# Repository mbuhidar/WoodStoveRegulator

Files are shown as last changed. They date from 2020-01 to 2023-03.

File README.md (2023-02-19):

# WoodStoveRegulator 2.3 - Arduino Powered Stove Damper Regulation

 System drives an Arduino microcontroller-based device that automatically 
 controls the air damper position on a wood stove in order to maintain a 
 constant exhaust pipe temperature.  
 
 System inputs: 
  1) Exhaust pipe temperature as measured by a thermocouple 
  mounted directly to the exhaust pipe (K-type thermocouple with 
  d-ring end connected to Arduino via MAX6675 module.
  2) A variable knob that controls LCD brightness (10K potentiometer).
  3) A variable knob that manually controls the stove damper 
  position between 0% and 100% for the first half of the knob rotation range
  and places the control system in automatic mode for potentiometer settings
  greater than half the rotation range. In automatic mode, the knob controls
  setting the stove target temperature between 100 C (212 F) and 200 C (392 F). 

 System outputs:
  1) LCD display showing:
     a) Exhaust pipe temperature and target temperature on 1st line of LCD.
     b) Alternating message on 2nd line of LCD showing A. damper / 
     potentiometer position and B. damper / mode - auto or manual.  
  2) Physical control of the stove air damper is transmitted from a 
     servo motor mounted inside the control unit with force and 
     position being transferred via sheathed control cable connected 
     between the servo and the stove damper lever.
  3) Passive buzzer that provides an audible alert when wood needs to be added
     or when stove damper will be closed due to end of fire event.

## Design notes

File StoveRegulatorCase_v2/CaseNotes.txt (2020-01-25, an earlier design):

3D Printed Case for Wood Stove Regulator

Configuration is wall mounted case with Arduino ports facing downward,
LCD screen centered vertically on the top case with control knobs below it.
Control cable exits the case on the bottom of the case as mounted.

Modeled using Autodesk Fusion 360 and printed using PLA filament.
Case was modified from:
Arduino-UNO-DIN-Case (6TE) (http://www.thingiverse.com/thing:3402441)
Changes to case and other printed parts:
- made bottom deeper to accommodate a breadboard shield for the Arduino
- added support ribbing to the top case to improve print quality
- changed holes and clamp in case to work with the push/pull cable and the thermocouple wire
- added a support mounting surface for the thermocouple amplifier
- added mounting pillars to support the servo inside the bottom case
- added a new wall mount and a cable connection piece for the wood stove damper

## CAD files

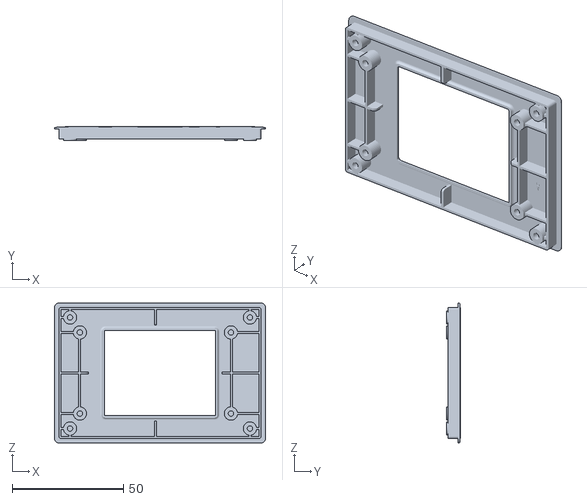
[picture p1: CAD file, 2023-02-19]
StoveRegulatorCase_v3/2.4-Bezel.STL
95.0 x 6.20 x 63.0

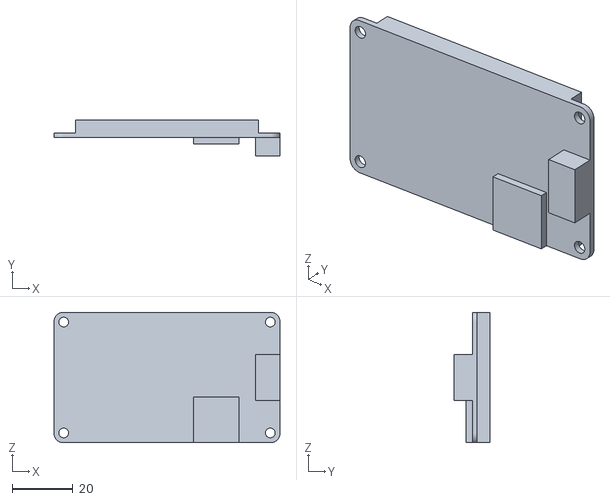
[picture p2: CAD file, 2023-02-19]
StoveRegulatorCase_v3/2.4-Display.STL
74.4 x 11.8 x 42.9

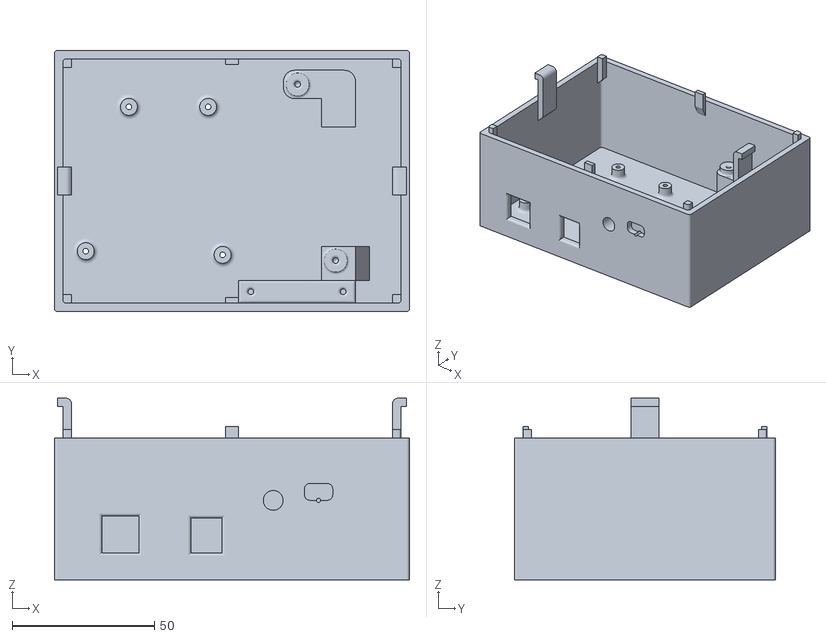
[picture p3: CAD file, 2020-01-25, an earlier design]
StoveRegulatorCase_v2/bottom_mod v21.stl
125.0 x 92.0 x 64.0

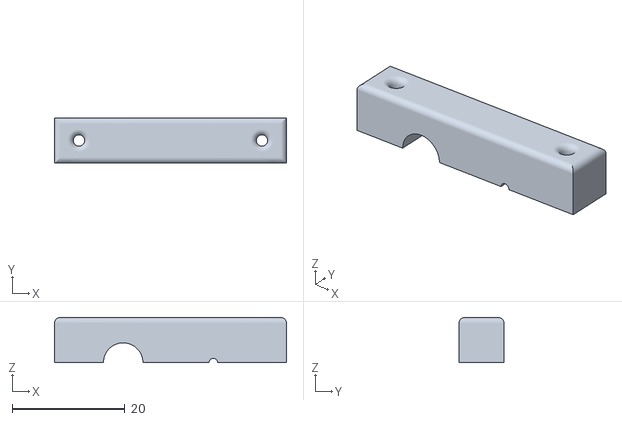
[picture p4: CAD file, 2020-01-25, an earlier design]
StoveRegulatorCase_v2/cable_clamp v1.stl
41.2 x 8.00 x 8.00

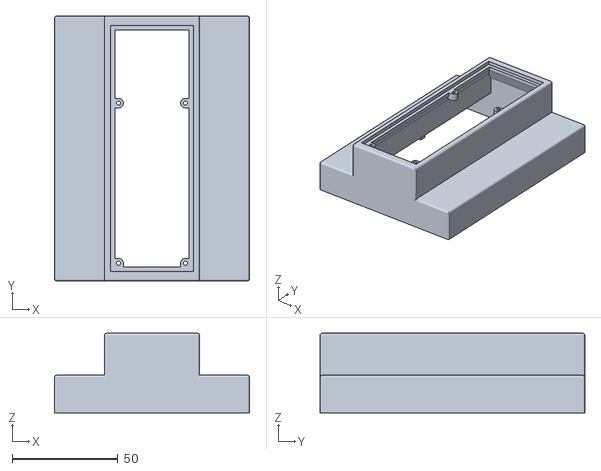
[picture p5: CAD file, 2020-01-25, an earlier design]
StoveRegulatorCase_v2/top_mod v2.stl
92.0 x 125.0 x 37.5

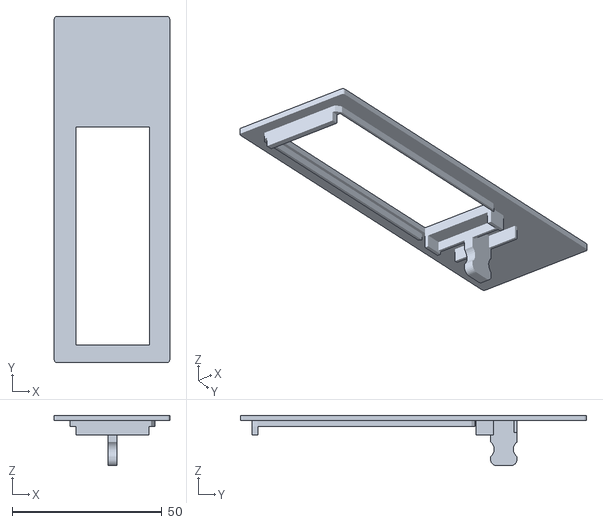
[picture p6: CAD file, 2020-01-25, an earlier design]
StoveRegulatorCase_v2/display_mod v1.stl
38.6 x 115.6 x 16.8

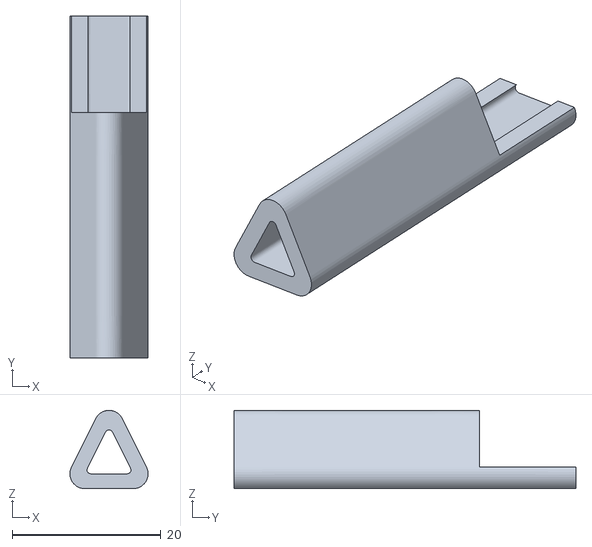
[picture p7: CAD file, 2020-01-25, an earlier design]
StoveRegulatorCase_v2/lever_adapter v1.stl
10.5 x 46.0 x 10.5

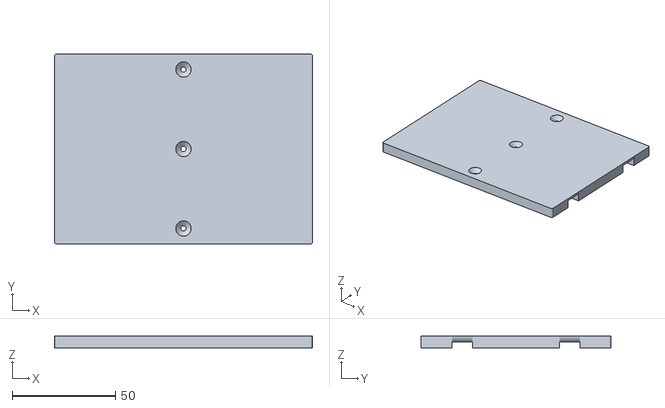
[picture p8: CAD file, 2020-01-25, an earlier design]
StoveRegulatorCase_v2/new_mount v2.stl
125.0 x 92.0 x 6.00

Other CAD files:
StoveRegulatorCase_v2/bottom_mod v21.f3d
StoveRegulatorCase_v2/cable_clamp v1.f3d
StoveRegulatorCase_v2/display_mod v1.f3d
StoveRegulatorCase_v2/lever_adapter v1.f3d
StoveRegulatorCase_v2/new_mount v2 v2.f3d
StoveRegulatorCase_v2/top_mod v2.f3d

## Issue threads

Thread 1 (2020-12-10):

Change left input knob to control temperature setting vs display brightness

mbuhidar, 2020-12-10:
Stove temp range can be 200-400 F, currently hard coded to 250 F.  Add control via left knob and add display for temperature set point.

Display setting can be hard coded vs using input pot.

mbuhidar, 2020-12-14:
Left potentiometer is does not act as an input for the controller, but acts as a variable resistor directly tied to the LCD brightness pin.  Would need to add another pot or repurpose the left knob and hardwire an appropriate resistor to manage LCD brightness.  Adjusted the hard coded set temperature to 275F in the meantime to raise the heat output of the stove.

mbuhidar, 2020-12-27:
May address this after winter if I rebuild the hardware.  In the meantime, will close this issue and open a new one to make the right pot act as a multi-function input to adjust temperature set point.

Closed 2020-12-27.

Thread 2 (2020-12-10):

After days of operation, controller went into 'stove empty - end fire' mode and opened damper while wood full and actively burning

mbuhidar, 2020-12-10:
This function was intended to be disabled, so need to understand how it was executed.  Suspect PID value accumulations over many days of continuous operation.

mbuhidar, 2020-12-10:
Switching from auto to manual mode and back to auto does not reset to eliminate this issue.  A power cycle was required to resolve the issue.

mbuhidar, 2020-12-14:
Completely rewrote the section of code that manages this functionality for v2.0 to resolve the issue.

Closed 2020-12-14.

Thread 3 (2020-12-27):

Add temperature set point adjustment feature using only available controller input - the right hand potentiometer.

mbuhidar, 2020-12-27:
Stove exhaust stack temp range can be 200-400 F, currently hard coded to 275 F in V2.0. Add control functionality via right knob via new 'adjust temperature set point' mode.  Need to determine user-initiated sequence to enter this mode and adjust the set point.

mbuhidar, 2021-01-18:
Feature to control set temperature was implemented by using the upper 50% of the potentiometer range for setting target temp and using the lower 50% of the range for manual damper control.  Temperature range available is set to 100 C (212 F) - 200 C (392 F).

Also, remapped the output display to add the temperature set point along with the prior messages.  Second line is set to rotate messages so all messages can be displayed.

Closed 2021-01-18.

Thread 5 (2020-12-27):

Add a function to check if the stove has been refilled with wood and is building temperature from low towards set point.

mbuhidar, 2020-12-27:
Current v2.0 code accumulates the integral parameter the entire time the exhaust stack temp is rising from a low temp towards the set point temp after a refill.  This results in the controller going into 'fill' mode inappropriately and in some cases, the controller can go into 'end' mode even when the temp is rising.  This is caused by the integral parameter building past the individual triggers for those two modes.

When the controller enters either of these two modes, the controller does not re-enter 'auto' mode until the temp reaches the set point.  This results in significant temp overshoot.  Even if the controller doesn't enter one of these modes, the integral windup can cause overshoot in 'auto' mode.

This new function / feature is intended to check for temp rise that would indicate stove refill and temperature build towards set point.  If refill condition is detected, the integral term should be reset to zero in order to prevent integral windup.

mbuhidar, 2020-12-31:
Added function that holds/updates an array of past six temp readings and compares average of first 3 to average of last 3 to determine if wood has been refilled.  The function is called to check status throughout the main loop function.

Closed 2020-12-31.

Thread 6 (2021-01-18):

Add physical switch to toggle between manual and auto mode.

mbuhidar, 2021-01-18:
Due to lack of physical user inputs to the controller, the single controller-attached potentiometer is being overused for mode and range selection.  The v2.2 code uses the upper half of the pot range to set the target temp in auto mode and the lower half of the pot range sets the damper position in manual mode.  The input range available is not ideal to control these modes and usage requires 'expert' knowledge of how the one knob works.

Need to add a physical input (push button switch?) to set and / or control auto mode vs manual mode.

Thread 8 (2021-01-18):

Rebuild controller using improved components and more robust internal connections

mbuhidar, 2021-01-18:
Current controller is printed with white filament and the LCD light and internal power supply lights bleed through the case.  Reprint case in black with provision for additional input button or pot per Issue #6.

Current internal connections are basic breadboard type connections.  These connections should made with soldered wires or a custom PCB.

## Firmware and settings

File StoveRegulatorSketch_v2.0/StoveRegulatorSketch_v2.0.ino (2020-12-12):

/*
 Wood Stove Regulator - Version 2.0
 by Michael Buhidar (GitHub: buhidar)

 with thanks to philco for many of the foundational ideas for this project
 (https://www.instructables.com/id/Wood-Stove-Regulator/)

 Sketch drives an Arduino microcontroller based system that auomatically 
 controls the air damper on a wood stove in order to maintain a 
 constant exhaust pipe temperature.  
 
 System inputs: 
  1) Exhaust pipe temperature as measured by a thermocouple 
  mounted directly to the exhaust pipe (sensor is K-type thermocouple with 
  d-ring end connected to Arduino via MAX6675 module.
  2) A variable knob that controls LCD brightness (10K potentiometer).
  3) A variable knob that manually controls the stove damper 
  position between 0% and 100% and places the control system in 
  automatic mode at potentiometer setting above 100% (10K potentiometer). 
  4) FUTURE FEATURE: A variable knob that controls the temperature target for
  the stove exhaust pipe.  Range from 200-400F.

 System outputs:
  1) LCD display showing:
     a) Exhaust pipe temperature on 1st line of LCD.
     b) Stove control knob potentiometer setting on 1st line of LCD.
     c) Damper position when in manual mode or in automatic
        mode while stove has adequate wood loaded on 2nd line of LCD.
     d) Message to refill the stove on 2nd line if wood is low or
        message that fire is ended if wood is not refilled.
  2) Physical control of the stove air damper transmitted from a 
     servo motor mounted inside the control unit with force and 
     position being transferred via sheathed control cable connected 
     between the servo and the stove damper lever.
  3) Passive buzzer that provides an audible alert when wood needs to be added
     or when stove damper will be closed due to end of fire event.

 
     
*/

// Include libraries for max6675, servo, LCD, and math.
#include <max6675.h>
#include <Servo.h>
#include <LiquidCrystal.h>
#include <math.h>

// Thermocouple pins mapping:
int thermoCsPort = 6;               // CS pin on MAX6675; chip select
int thermoSoPort = 7;               // SO pin of MAX6675; serial output
int thermoSckkPort = 8;             // SCK pin of MAX6675; serial clock input

// int units = 1;                      // Toggle for readout temp units (0 = ˚F, 1 = ˚C) 
float error = 0.0;                  // Temperature compensation error

// Buzzer variables:
int buzzerPort = 9;                 // Buzzer port
int buzzerRefillFrequency = 1900;   // Buzzer tone frequency for refill alarm
int buzzerRefillRepeat = 3;         // Number of refill alarm tones
int buzzerRefillDelay = 1000;       // Delay of refill alarm tone
int buzzerCloseFrequency = 950;    // Buzzer tone frequency for end of fire damper close alarm
int buzzerCloseRepeat = 2;          // Number of tones for end of fire damper close alarm
int buzzerCloseDelay = 2000;        // Delay of tone for end of fire damper close alarm

// Potentiometer variables
int servoPort = 0;
int potPort = 0;

// LCD port variables
int lcdPort1 = 12;
int lcdPort2 = 11;
int lcdPort3 = 5;
int lcdPort4 = 4;
int lcdPort5 = 3;
int lcdPort6 = 2;

// Device objects
Servo myservo;  // create servo object to control the servo
MAX6675 thermocouple(thermoSckkPort, thermoCsPort, thermoSoPort); 
LiquidCrystal lcd(lcdPort1, lcdPort2, lcdPort3, lcdPort4, lcdPort5, lcdPort6);

// Servo settings
float servoCalibration = 1.0;  // 1.0 is neutral cal - adjust value so servo arm drives closed damper when damper variable equals 0 (0%)
float servoOffset = 20;  // offset angle for servo angle adjustment
float servoAngle = 100;  // adjust value to define total angular travel of servo so that cable drives damper from fully opened to fully closed

// Regulation variables (Based on PID):
// damper = kP * errP + kI * errI + kD * errD
// errP = targetTempC - temperature
// errI = errP integral
// errD = errP derivative
int temperature = 0;  // initialize temperature variable for C
int temperatureF = 32; // initialize temperature variable for F - only used for display output
float temperatureMin = 38; // under this temperature (38C = 100F), the regulation starts an integral measure to estimate end of fire and close the damper
float targetTempC = 121.1; // the target temperature as measured by the thermocouple (121.1 C = 250 F)
float errP = 0.0;
float errD = 0.0;
float errI = 0.0;
float errOld = 0.0;
float kP = 5;              // P coefficient of the PID regulation
float kI = 0.0005;         // I coefficient of the PID regulation
float kD = 0.00005;        // D coefficient of the PID regulation

float refillTrigger = 5000;    // refillTrigger used to notify need of a wood refill
float closeTrigger = 15000;    // closeTrigger used to close damper at end of combustion

int pot = 0;
int oldPot = 0;
float potMax = 1023.0;   // Potentiometer calibration
int potRelMax = 100;     // Potentiometer value above which the regulator runs in automatic mode

int angle = 0;
int damper = 0;
int oldDamper = 0;
int diff = 0;
float maxDamper = 100.0;  // Sets maximum damper setting
float minDamper = 0.0;    // Sets minimum damper setting
float zeroDamper = 0.0;   // Sets zero damper setting - note that stove allows some amount of airflow at zero damper

String messageTemp; // Initialize message for temperature output
String messageDamp; // Initialize message for damper setting output

boolean closeBuzzer = true;
boolean refillBuzzer = true;




void setup() {
  Serial.begin(9600);  // opens serial port, sets data rate to 9600 bps
  myservo.attach(10);  // attach servo variable to pin 10
  // move servo from current angle to zero non-abruptly
  ang = myservo.read();
  for (int i = ang; i > 0; i--) {
    myservo.write(ang);
    delay(200);
  myservo.write(0);    // write 0 deg angle to servo after gradual move
  myservo.detach();    // detach servo variable from its pin
  lcd.begin(16, 2);    // initializes 1602 LCD screen for 16 columns and 2 rows
  pinMode(buzzerPort, OUTPUT); // configures buzzer pin as an output
}




void loop() {

  temperature = thermocouple.readCelsius();
  temperatureF = temperature * 9 / 5 + 32;  // convert C to F
  
  delay(500); 
  
  if (temperature == -1) {
    Serial.println("Thermocouple Error!!"); // Temperature is read as -1 and there is a thermocouple error
  } else {

    pot = analogRead(potPort); // reads the value of the potentiometer (value between 0 and 1023)
    pot = map(pot, 0, potMax, 0, 105); // scale potentiometer reading to 0 to 105%; note that setting above 100% invokes automatic mode
    
    if (pot <= potRelMax ) {  
      // Manual damper regulation mode
      errI = 0;  // reset integral term
      errD = 0;  // reset derivative term
      closeBuzzer = true;
      refillBuzzer = true;
      damper = round(pot * maxDamper / 100);  // scales damper setting according to max setting
      messageDamp = "Damper=" + String(damper) + "% Man";
    }

    else
    
    { 
      if (errI < closeTrigger) {
        // Automatic PID regulation
        errP = targetTempC - temperature;  // set proportional term
        errI = errI + errP;                // update integral term
        errD = errP - errOld;              // update derivative term
        errOld = errP;
        // set damper position and limit damper values to physical constraints
        damper = kP * errP + kI * errI + kD * errD;
        if (damper < minDamper) damper = minDamper;
        if (damper > maxDamper) damper = maxDamper;


        // Close and end fire
        // if (errI >= closeTrigger) errI = closeTrigger;
        // 
        if (temperature < temperatureMin) errI = 0;  // reset errI if temperature is higher than minimum cutoff temperature
        // if (errI >= closeTrigger) damper = zeroDamper;

        messageDamp = "Damper=" + String(damper) + "% Auto";
        //Refill Alarm
        if (errI > refillTrigger) {
          messageDamp = "Damper=" + String(damper) + "% Fill";
          if (refillBuzzer) {
            for (int i = 0; i < buzzerRefillRepeat; i++) {
              tone(buzzerPort, buzzerRefillFrequency);
              delay(buzzerRefillDelay);
              noTone(buzzerPort);
              delay(buzzerRefillDelay);
            }
            refillBuzzer = false;
          }
          if (temperature > targetTempC) {
            errI = 0;
            errD = 0;
            refillBuzzer = true;
          }
        }

      }

      else {
        // Close Damper if end of combustion
        messageDamp = "Damper=" + String(damper) + "% End";

        if (closeBuzzer) {
          for (int i = 0; i < buzzerCloseRepeat; i++) {
            tone(buzzerPort, buzzerCloseFrequency);
            delay(buzzerCloseDelay);
            noTone(buzzerPort);
            delay(buzzerCloseDelay);
          }
          closeBuzzer = false;
        }
      }
    }

    // Display messages on LCD
    lcd.clear();
    lcd.setCursor(0, 0);
    messageTemp = "Tmp=" + String(temperatureF) + "F" + " Pot=" + round(pot) + "%";
    lcd.print(messageTemp);
    lcd.setCursor(0, 1);
    lcd.print(messageDamp);

    // Serial Plotter
    Serial.print(round(damper/maxDamper * 100));
    Serial.print(",");
    Serial.print(temperatureF);
    Serial.print(",");
    Serial.print(errP);
    Serial.print(",");
    Serial.print(errI);
    Serial.print(",");
    Serial.print(errD);
    Serial.print(",");    
    Serial.println();

    // Turn servo only for more than 2° delta
    diff = damper - oldDamper;
    if (abs(diff) > 2) {
      lcd.print(" x");
      delay(500);
      myservo.attach(10);
      if (diff > 2) {
        for (int i = 0; i < diff; i++) {
            angle = (oldDamper + i + 1) * servoAngle / (maxDamper * servoCalibration) - servoOffset;
            myservo.write(angle);
            delay(200);
          }
      }
      
      if (diff < 2) {
        for (int i = 0; i < abs(diff); i++) {
            angle = (oldDamper - i - 1) * servoAngle / (maxDamper * servoCalibration) - servoOffset;
            myservo.write(angle);
            delay(200);
          }
      }
          
      myservo.detach();

      oldPot = pot;
      oldDamper =  damper;
    }
    delay(4000);
  }
}

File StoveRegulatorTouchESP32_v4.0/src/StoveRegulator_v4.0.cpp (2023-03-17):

/*
 Wood Stove Regulator - Version 4.0 
 Copyright (C) 2020  Michael Buhidar (GitHub: mbuhidar)
 
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
 For a copy of the GNU General Public License, 
 see <https://www.gnu.org/licenses/>.

 With thanks to philco for many of the foundational ideas for this project
 (https://www.instructables.com/id/Wood-Stove-Regulator/)

 The code drives an ESP32 microcontroller based system that automatically 
 controls the air damper on a wood stove in order to maintain a constant
 exhaust pipe temperature.  
 
 System inputs and outputs: 

  1) Exhaust pipe temperature as measured by a thermocouple mounted directly to
     the exhaust pipe. Sensor is K-type thermocouple with a ring attach end
     connected to an Arduino (Uno in this case) via MAX6675 module.

  2) A touch screen display (Nextion NX3224T024_011) that has two modes - 
     automatic and manual.  

     - Automatic Mode: 
          Screen displays the damper position as a percentage (0-100%), the
          exhaust pipe temperature as an integer (deg F), and the target
          temperature as an integer (deg F). The screen also has in input
          slider bar that can be used to set the target temperature. The damper
          position is automatically controlled by the Arduino microcontroller
          based on the exhaust pipe temperature in this mode. There is a button
          that can be pressed to move to manual mode and display the manual
          mode screen.  
     - Manual Mode:
          Screen displays the damper position as a percentage (0-100%) and the
          exhaust pipe temperature as an integer (deg F). The target
          temperature is greyed out in this mode since it cannot be set on this
          screen. The damper position in this mode is is directly controlled by
          input slider bar on the screen. There is a button that can be pressed
          to move to automatic mode and display the automatic mode screen.
     - TODO: Both modes:
          There is an indicator that flashed when wood needs to be added to the 
          stove. A buzzer is also used to provide an audible alert when wood
          needs to be added.

  3) Physical control of the stove air damper transmitted from a servo motor 
     mounted inside the control unit with force and position being transferred
     via sheathed control cable connected between the servo and the stove
     damper lever.

  4) TODO: Passive buzzer that provides an audible alert when wood needs to be
     added or when stove damper will be closed due to end of fire event.
*/

// ****************************************************************************
// Note: This code is written for the Arduino Uno microcontroller, however,
// more than one hardware serial bus is needed for this project if serial
// output for data analysis is needed. The Arduino Uno only has one hardware
// serial bus. Code could be used for other Arduino microcontrollers that have
// more than one hardware serial bus, but the code would need to be modified.
// ****************************************************************************

// Include libraries for Arduino, max6675, servo, math, and software serial.

#include <Arduino.h>
#include <max6675.h>
#include <Servo.h>
#include <math.h>

// ****************************************************************************
// Device setup and initialization:
// ****************************************************************************

// Software Serial pin mapping variables:
const int rxPort = 10;               // RX pin on Arduino
const int txPort = 11;               // TX pin on Arduino

// Thermocouple pin mapping variables and compensation error variable:
const int thermoCsPort = 6;         // CS pin on MAX6675; chip select
const int thermoSoPort = 7;         // SO pin of MAX6675; serial output
const int thermoSckkPort = 8;       // SCK pin of MAX6675; serial clock input
float error = 0.0;                  // Temperature compensation error

// Buzzer setup variables:
/*
// Buzzer port id
int buzzerPort = 9;
// Buzzer tone frequency for refill alarm
int buzzerRefillFrequency = 1900;
// Number of refill alarm tones
int buzzerRefillRepeat = 3;
// Delay between refill alarm tones
int buzzerRefillDelay = 1000;
// Buzzer tone frequency for end of fire damper close alarm
int buzzerEndFrequency = 950;
// Number of tones for end of fire damper close alarm
int buzzerEndRepeat = 2;
// Delay of tone for end of fire damper close alarm
int buzzerEndDelay = 2000;
*/

// Device objects - create servo and thermocouple objects 
Servo myservo;
MAX6675 thermocouple(thermoSckkPort, thermoCsPort, thermoSoPort); 
SoftwareSerial Serial2(rxPort, txPort); // RX, TX

// Servo calibration settings:
// Servo rate calibration: neutral calibration is 1.0 - adjust value so servo
// arm drives closed damper when damper variable equals 0 (0%)
float servoCalibration = 1.0;
// offset angle for servo angle adjustment
float servoOffset = -20;
// adjust value to define total angular travel of servo so that cable drives
// damper from fully opened to fully closed
float servoRange = 100;

// Temperature variables:       
// Initialize temperature variable (50F = 10C)
int tempF = 50;
// Under this temperature (100F = 38C), the regulation closes the damper
// if end of fire conditions are met
int tempFMin = 100;
// Target temperature (275F = 135C)
int targetTempF = 275;

// PID regulation variables:
float errP = 0.0;          // initialize the proportional term
float errD = 0.0;          // initialize the derivative term
float errI = 0.0;          // initialize the integral term
float errOld = 0.0;        // initialize term used to capture prior cycle ErrP
float kP = 5.0;            // P coefficient of the PID regulation
float tauI = 1000;           // Integral time constant (sec/repeat)
float tauD = 5;              // Derivative time constant (sec/reapeat)
float kI = kP/tauI;        // I coefficient of the PID regulation
float kD = kP/tauD;        // D coefficient of the PID regulation

// Refill and end of fire variables:
// refillTrigger used to notify need of a wood refill
//float refillTrigger = 5000;
// closeTrigger used to close damper at end of combustion
float endTrigger = 25000;

// Damper variables:
int angle = 0;
int damper = 0;
int targetDamper = 0;
int diff = 0;
float maxDamper = 100;  // Sets maximum damper setting
float minDamper = 0.0;    // Sets minimum damper setting
float zeroDamper = 0.0;   // Sets zero damper setting
// Note that stove allows some amount of airflow at zero damper

//bool endBuzzer = true;
//bool refillBuzzer = true;

 // Setup temperature history array
float tempHist[6] = {0, 0, 0, 0, 0, 0};

// NOTE : String used to add end chars to the data sent to the Nextion Display
//        and to verify the end of the string for incoming data.
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

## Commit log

2020-01-25 Add Arduino sketch, case model files, and PID data file.
    [PID Model for StoveRegulator.xlsx, bottom_mod v21.f3d, cable_clamp v1.f3d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]
2020-01-25 Add 3D printer .stl file for botttom case.
    [bottom_mod v21.stl]
2020-01-25 Small change to PID model file.
    [PID Model for StoveRegulator.xlsx]
2020-01-25 Added sketch notes.txt file to track desired sketch improvements.
2020-01-26 Added serial outputs for PID error terms to sketch.
2020-01-26 Add stove data logs.
    [012520-1.xlsx, 012520-10.xlsx, 012520-11.xlsx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]
2020-12-20 Add temp check to end fire logic and increase PID coefficients
2020-12-21 Changed PID coefficients for more aggressive control.
    [012520-1.xlsx, 012520-10.xlsx, 012520-11.xlsx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]
2020-12-31 Corrected calculation of serial output values.
    [122820-all.xlsx]
2021-01-17 Rework sketch directory structure and add v2.2 for feature expansion
    [StoveRegulator_v1.0.ino, StoveRegulator_v2.0.ino, StoveRegulator_v2.1.ino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]
2021-01-18 Add temp setting feature - closes Issue #3
    [StoveRegulator_v2.2.ino]
2021-01-18 Fixed a logic error in the WoodFilled() function
    [StoveRegulator_v2.2.ino]
2021-11-29 Fix doc for v2.2 README and Sketch.
    [StoveRegulator_v2.2.ino]
2023-02-08 Add breadboard view, schematic view, and fritzing file.
    [stove_arduino_fritzing_v1.0.0.fzz]
2023-02-10 Update fritzing file.
    [stove_arduino_fritzing_v1.0.0.fzz]
2023-02-10 Update breadboard and schematic images; fix typo in cpp file.
    [StoveRegulator_v2.3.cpp]
2023-02-19 Create directories for the touch screen version (v3) of the regulator.
    [2.4-Bezel.STL, 2.4-Display.STL, bottom_mod v21.f3d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]
2023-03-02 Fix variable types to prevent integer math rounding issues.
    [StoveRegulator_v3.x_alpha.cpp]
2023-03-06 Add display code and refine regulator code.
2023-03-12 Revert back to SoftwareSerial dedicated port.
    [StoveRegulator_v3.x_alpha.cpp]
2023-03-17 Start regulator code for ESP32.

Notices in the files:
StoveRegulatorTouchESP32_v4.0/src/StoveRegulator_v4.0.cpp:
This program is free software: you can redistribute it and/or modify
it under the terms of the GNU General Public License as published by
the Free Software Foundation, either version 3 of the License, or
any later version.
